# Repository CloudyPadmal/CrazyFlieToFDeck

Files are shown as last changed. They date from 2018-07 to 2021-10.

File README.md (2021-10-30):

# CrazyFlieToFDeck

This repository contains KiCAD source files and generated gerber files for **CrazyFlie Obstacle Avoidance Sensor Deck**.



<table>
<tr>
<th>Front View</td>
<th>Bottom View</td>
</tr>
<tr>
<td></td>
<td></td>
</tr>
</table>

## Time of Flight Sensor



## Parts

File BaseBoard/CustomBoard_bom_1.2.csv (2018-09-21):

Component | Description | Part | References | Value | Footprint | Quantity Per PCB | Datasheet
1 | Unpolarized capacitor | C_Small | C1 C2 | 100n | C_0603 | 2
2 | Unpolarized capacitor | C_Small | C3 | 4.7u | C_0603 | 1
3 | LED generic, alternativ symbol | LED_ALT | D1 | POWER_LED | LED_0603 | 1
4 | Generic connector, single row, 01x05 | Conn_01x05 | J15 | Camera | AMGCam | 1
5 | Generic connector, single row, 01x10 | Conn_01x10 | J2 | LEFT | BF090-10-X-B2 | 1
6 | Generic connector, single row, 01x10 | Conn_01x10 | J1 | RIGHT | BF090-10-X-B2 | 1
7 | Generic connector, single row, 01x05 | Conn_01x05 | J3 | Sensor01 | SensorPads | 1
8 | Generic connector, single row, 01x05 | Conn_01x05 | J4 | Sensor02 | SensorPads | 1
9 | Generic connector, single row, 01x05 | Conn_01x05 | J5 | Sensor03 | SensorPads | 1
10 | Generic connector, single row, 01x05 | Conn_01x05 | J6 | Sensor04 | SensorPads | 1
11 | Generic connector, single row, 01x05 | Conn_01x05 | J7 | Sensor05 | SensorPads | 1
12 | Generic connector, single row, 01x05 | Conn_01x05 | J8 | Sensor06 | SensorPads | 1
13 | Generic connector, single row, 01x05 | Conn_01x05 | J9 | Sensor07 | SensorPads | 1
14 | Generic connector, single row, 01x05 | Conn_01x05 | J10 | Sensor08 | SensorPads | 1
15 | Generic connector, single row, 01x05 | Conn_01x05 | J11 | Sensor09 | SensorPads | 1
16 | Generic connector, single row, 01x05 | Conn_01x05 | J12 | Sensor10 | SensorPads | 1
17 | Generic connector, single row, 01x05 | Conn_01x05 | J13 | Sensor11 | SensorPads | 1
18 | Generic connector, single row, 01x05 | Conn_01x05 | J14 | Sensor12 | SensorPads | 1
19 | Resistor | R | R2 R3 R4 R5 R6 R7 R8 R9 R10 R11 R12 R13 R14 | 10k | R_0603 | 13
20 | Resistor | R | R1 | 2k | R_0603 | 1
21 |  | DS28E05 | U1 | DS28E05 | SOT-23 | 1
22 |  | PCA9555X | U2 | PCA9555X | TSSOP-24_4.4x7.8mm_Pitch0.65mm | 1 | https://www.mouser.com/datasheet/2/302/PCA9555A-1127572.pdf
23 |  | VL53L1X | U3 | VL53L1X | VL53L1X | 1
Component Groups: | 23
Component Count: | 36
Fitted Components: | 36
Number of PCBs: | 1
Total components: | 36
Schematic Version: | 1.2
Schematic Date: | 2018-07-24
BoM Date: | Sat 11 Aug 2018 04:17:48 PM +0530
Schematic Source: | /home/knight/Documents/KiCAD/FinalBoards/CrazyFlieCustomBoardBase/CustomBoard.sch
KiCad Version: | Eeschema 4.0.7-e2-6376~58~ubuntu16.04.1

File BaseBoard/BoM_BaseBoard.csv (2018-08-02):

Component | Description | Part | References | Value | Footprint | Quantity Per PCB | Datasheet
1 | Unpolarized capacitor | C_Small | C1 C2 | 100n | C_0402 | 2
2 | Unpolarized capacitor | C_Small | C3 | 4.7u | C_0402 | 1
3 | LED generic, alternativ symbol | LED_ALT | D1 | POWER_LED | LED_0402 | 1
5 | Generic connector, single row, 01x10 | Conn_01x10 | J2 | LEFT | BF090-10-X-B2 | 1
6 | Generic connector, single row, 01x10 | Conn_01x10 | J1 | RIGHT | BF090-10-X-B2 | 1
19 | Resistor | R | R2 R3 R4 R5 R6 R7 R8 R9 R10 R11 R12 R13 R14 | 10k | R_0402 | 13
20 | Resistor | R | R1 | 2k | R_0402 | 1
21 |  | DS28E05 | U1 | DS28E05 | SOT-23 | 1
22 |  | PCA9555 | U2 | PCA9555 | QFN-24_4x4mm_Pitch0.5mm | 1
23 |  | VL53L1X | U3 | VL53L1X | VL53L1X | 1
Component Groups: | 23
Component Count: | 36
Fitted Components: | 36
Number of PCBs: | 1
Total components: | 36
Schematic Version: | 1.2

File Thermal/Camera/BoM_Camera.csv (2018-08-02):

Component | Description | Part | References | Value | Footprint | Quantity Per PCB | Datasheet
1 | Unpolarized capacitor | C_Small | C3 | 1.5u | C_0603 | 1
2 | Unpolarized capacitor | C_Small | C1 | 10u | C_0603 | 1
3 | Unpolarized capacitor | C_Small | C2 | 1u | C_0603 | 1
7 | Resistor | R | R1 R2 R3 | 10k | R_0402 | 3
8 | Resistor | R | R4 | 20R | R_0402 | 1
9 | Camera module | AMG8833 | U1 | AMG8833 | AMG8833 | 1
Component Groups: | 9
Component Count: | 11
Fitted Components: | 11
Number of PCBs: | 1
Total components: | 11

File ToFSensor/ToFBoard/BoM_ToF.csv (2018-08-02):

Component | Description | Part | References | Value | Footprint | Quantity Per PCB | Datasheet
1 | Unpolarized capacitor | C_Small | C1 | 100n | C_0402 | 1
2 | Unpolarized capacitor | C_Small | C2 | 4.7u | C_0402 | 1
5 | ToF sensor | VL53L1X | U1 | VL53L1X | VL53L1X | 1
Component Groups: | 5
Component Count: | 5
Fitted Components: | 5
Number of PCBs: | 1
Total components: | 5

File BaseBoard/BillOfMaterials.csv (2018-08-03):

Designator | MPN/Seed SKU | Qty | Price | Total
C6 | GRM033R60J155ME14EA01 | 1 | 0.33 | 0.33
C1 C2 C7 C9 C11 C13 C15 C17 C19 C21 C23 C25 C27 C29 C31 C33 C35 | CBR04C108B5GAC | 17 | 0.056 | 0.952
C4 | C1608X5R0J106K080AE | 1 | 0.32 | 0.32
C5 | 885012106003 | 1 | 0.1 | 0.1
C3 C8 C10 C12 C14 C16 C18 C20 C22 C24 C26 C28 C30 C32 C34 C36 | C1005X5R0J475K050BC | 16 | 0.35 | 5.6
D1 | SMLP13BC8TT86 | 1 | 0.4 | 0.4
J2 | BF090-10-X-B2 | 1 | 0.5 | 0.5
J1 | BF090-10-X-B2 | 1 | 0.5 | 0.5
R2 R3 R4 R5 R6 R7 R8 R9 R10 R11 R12 R13 R14 R15 R16 R17 | RT0402BRC0710KL | 16 | 0.349 | 5.584
R18 | RCS040220R0FKED | 1 | 0.11 | 0.11
R1 | CRCW04022K00JNEDC | 1 | 0.1 | 0.1
U4 | AMG8833 | 1 | 22.16 | 22.16
U1 | DS28E05R+T | 1 | 0.88 | 0.88
U2 | PCA9555BS,118 | 1 | 2.14 | 2.14
U3 U5 U6 U7 U8 U9 U10 U11 U12 U13 U14 U15 U16 U17 U18 U19 | VL53L1CXV0FY/1 | 16 | 5.81 | 92.96
 |  |  |  | 132.636

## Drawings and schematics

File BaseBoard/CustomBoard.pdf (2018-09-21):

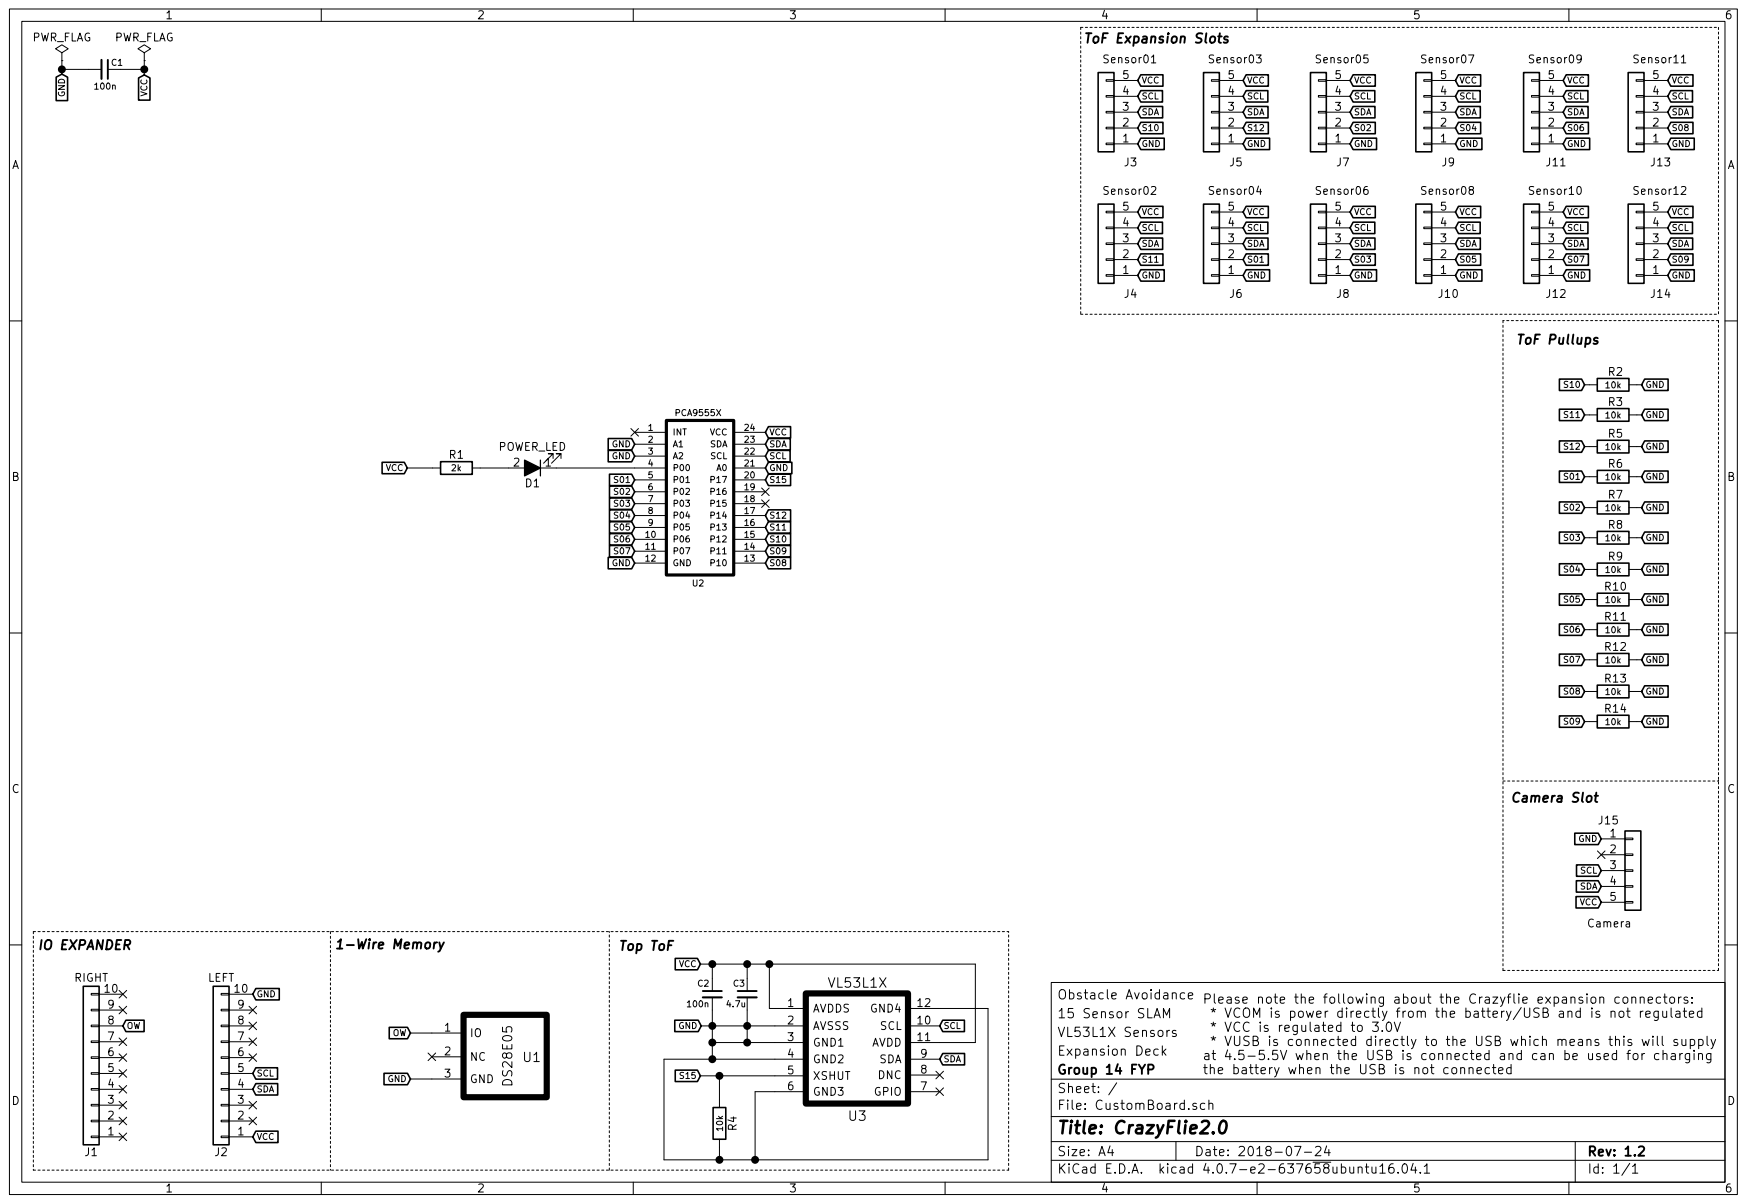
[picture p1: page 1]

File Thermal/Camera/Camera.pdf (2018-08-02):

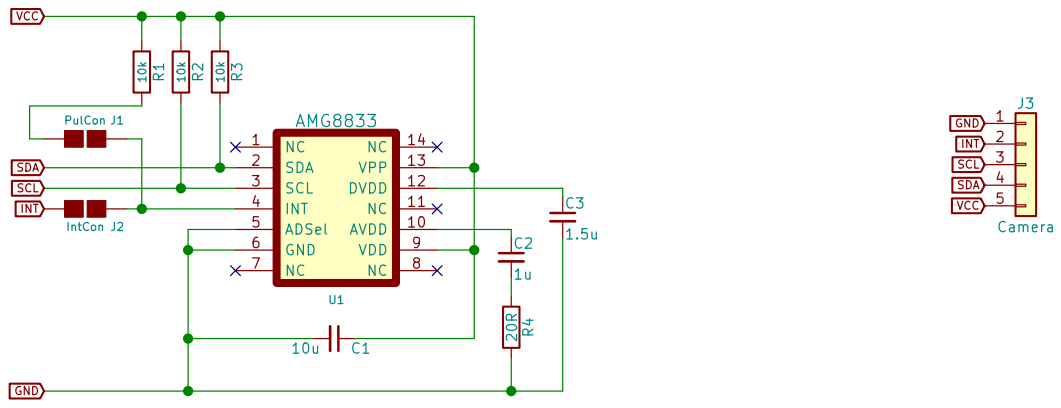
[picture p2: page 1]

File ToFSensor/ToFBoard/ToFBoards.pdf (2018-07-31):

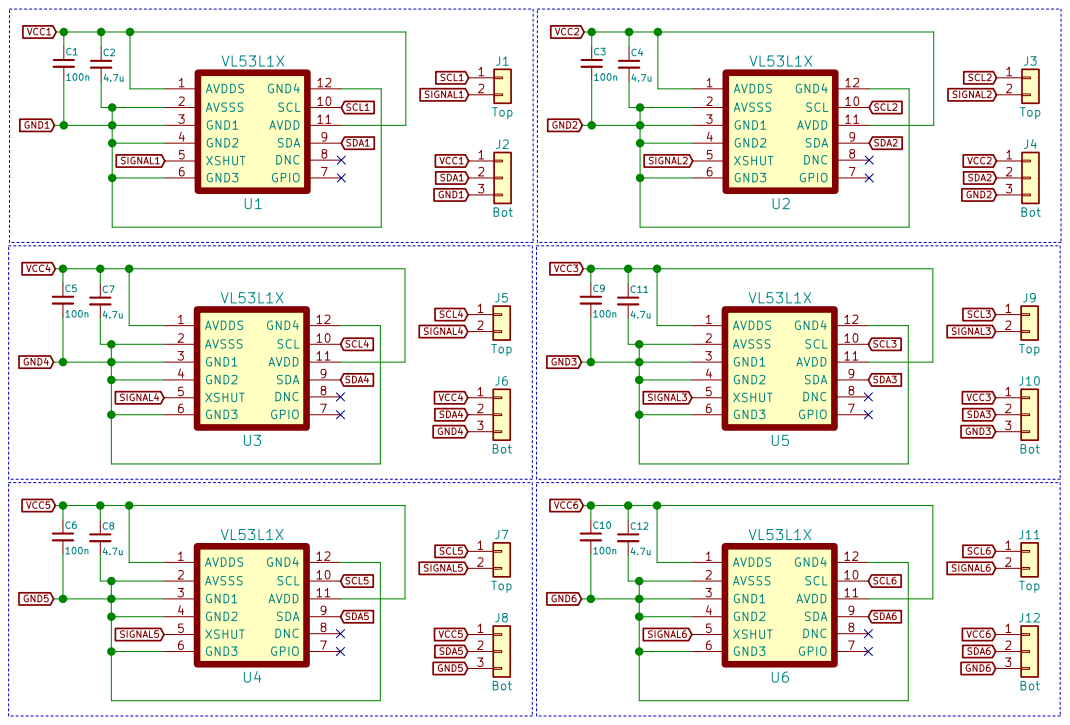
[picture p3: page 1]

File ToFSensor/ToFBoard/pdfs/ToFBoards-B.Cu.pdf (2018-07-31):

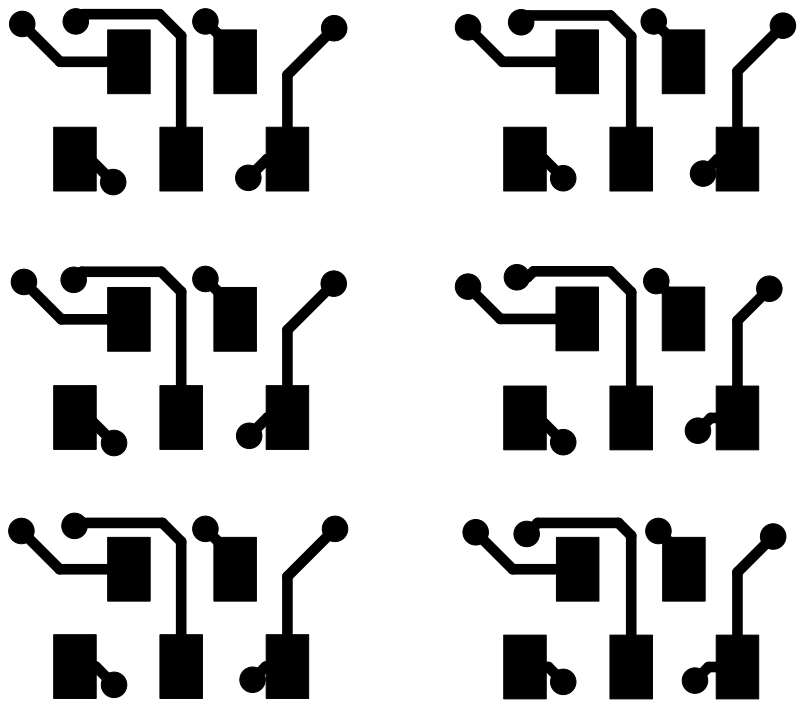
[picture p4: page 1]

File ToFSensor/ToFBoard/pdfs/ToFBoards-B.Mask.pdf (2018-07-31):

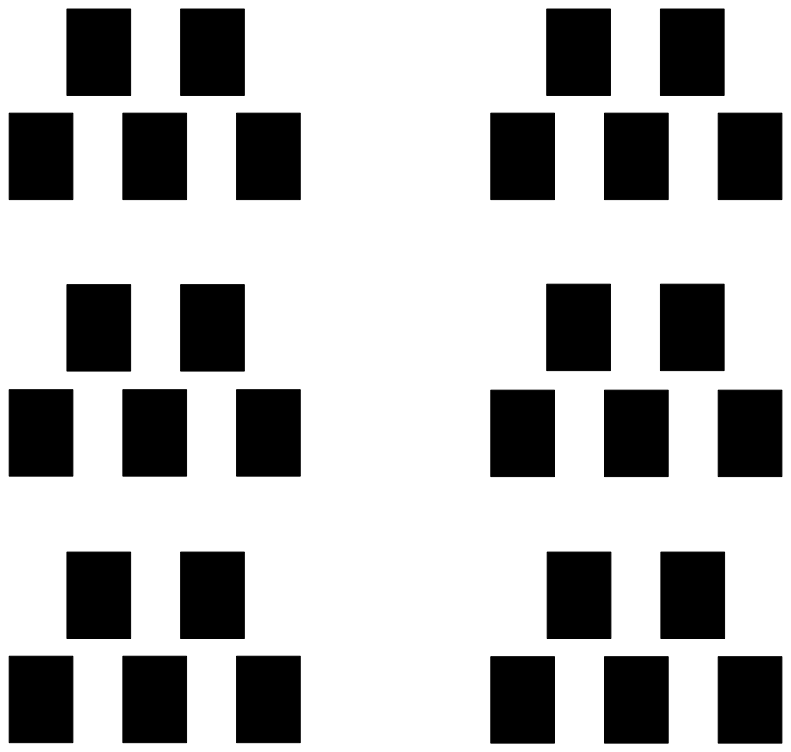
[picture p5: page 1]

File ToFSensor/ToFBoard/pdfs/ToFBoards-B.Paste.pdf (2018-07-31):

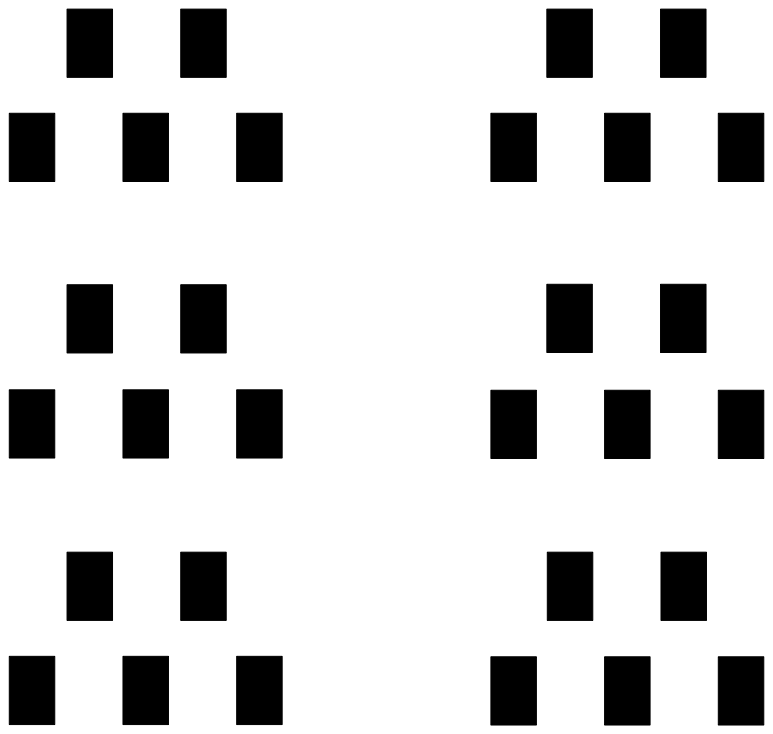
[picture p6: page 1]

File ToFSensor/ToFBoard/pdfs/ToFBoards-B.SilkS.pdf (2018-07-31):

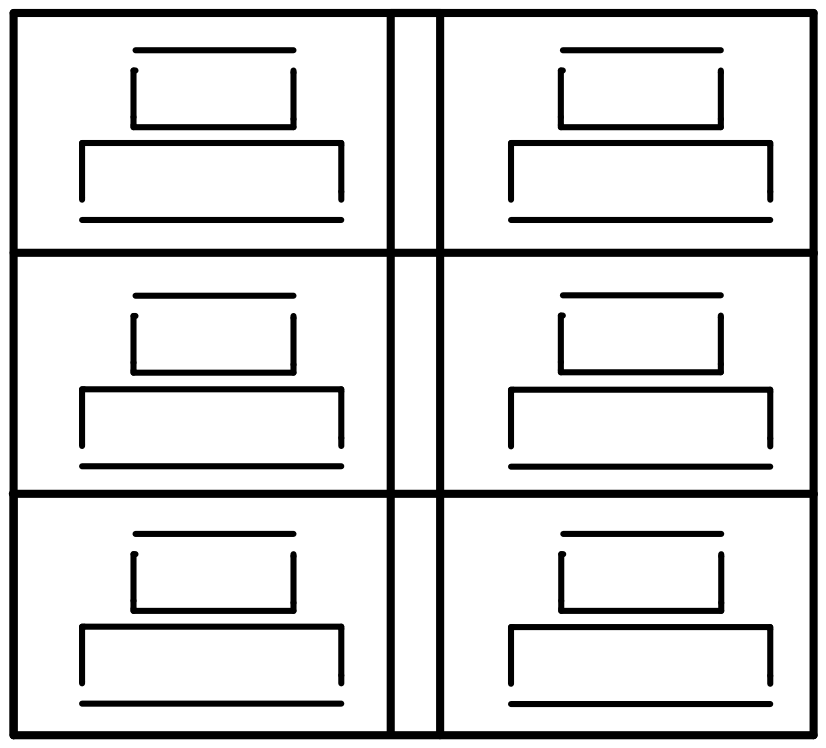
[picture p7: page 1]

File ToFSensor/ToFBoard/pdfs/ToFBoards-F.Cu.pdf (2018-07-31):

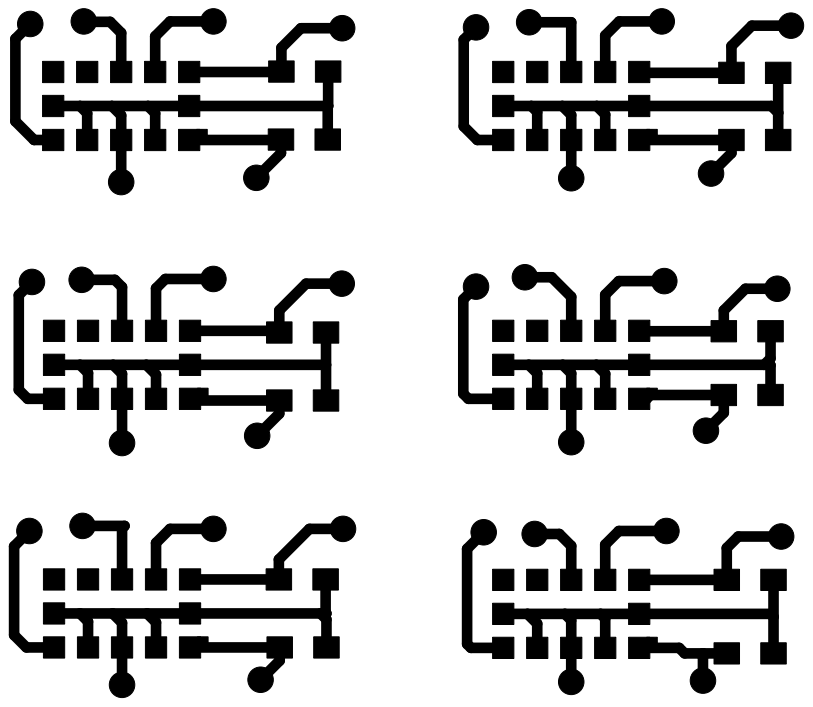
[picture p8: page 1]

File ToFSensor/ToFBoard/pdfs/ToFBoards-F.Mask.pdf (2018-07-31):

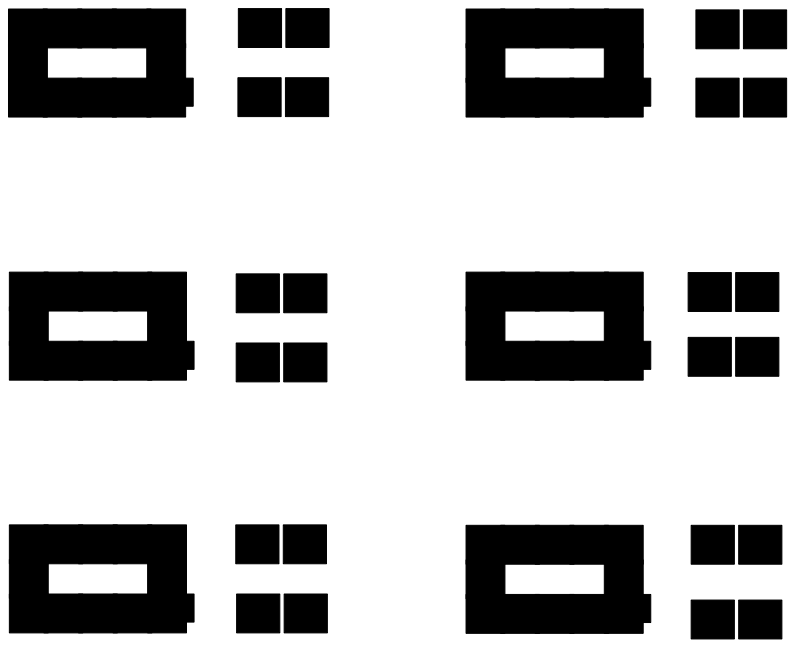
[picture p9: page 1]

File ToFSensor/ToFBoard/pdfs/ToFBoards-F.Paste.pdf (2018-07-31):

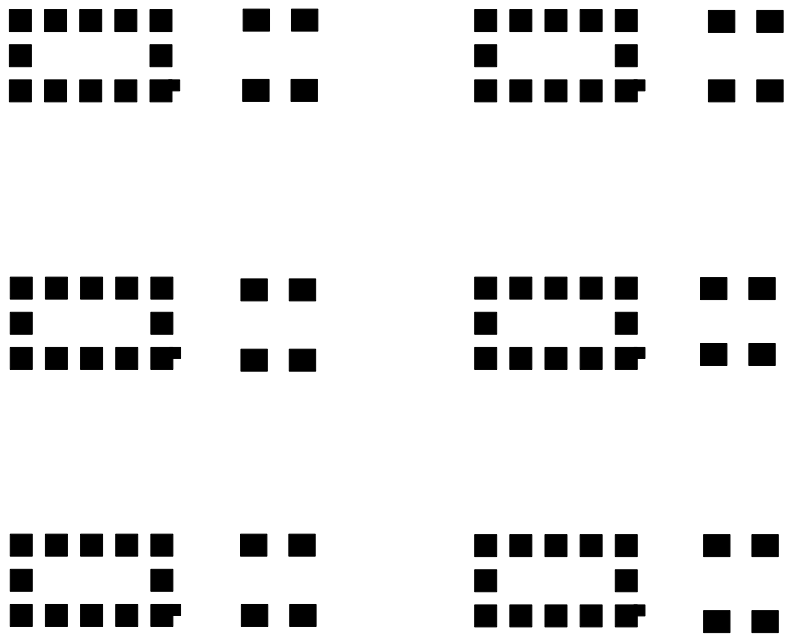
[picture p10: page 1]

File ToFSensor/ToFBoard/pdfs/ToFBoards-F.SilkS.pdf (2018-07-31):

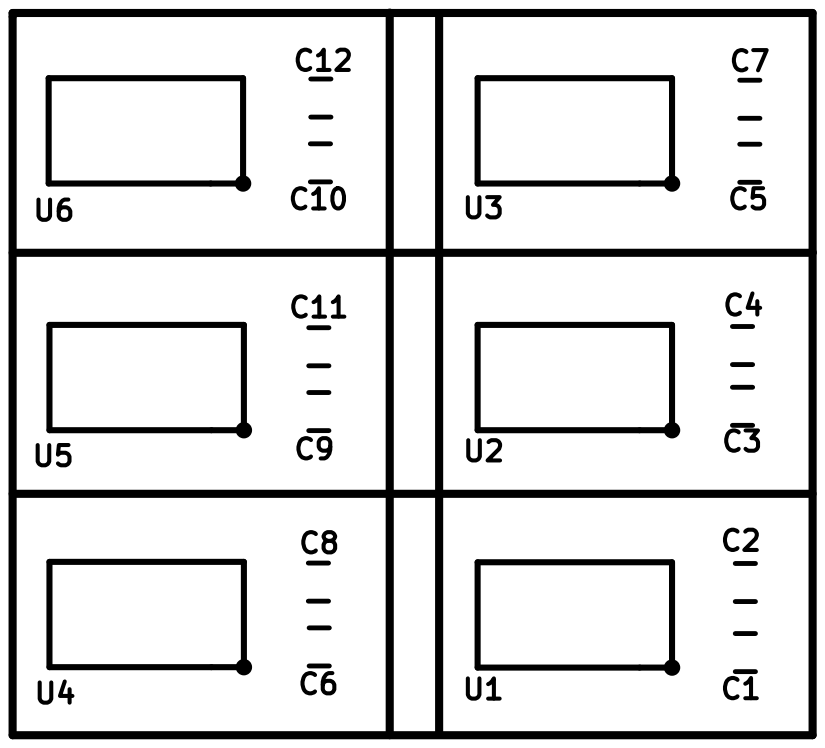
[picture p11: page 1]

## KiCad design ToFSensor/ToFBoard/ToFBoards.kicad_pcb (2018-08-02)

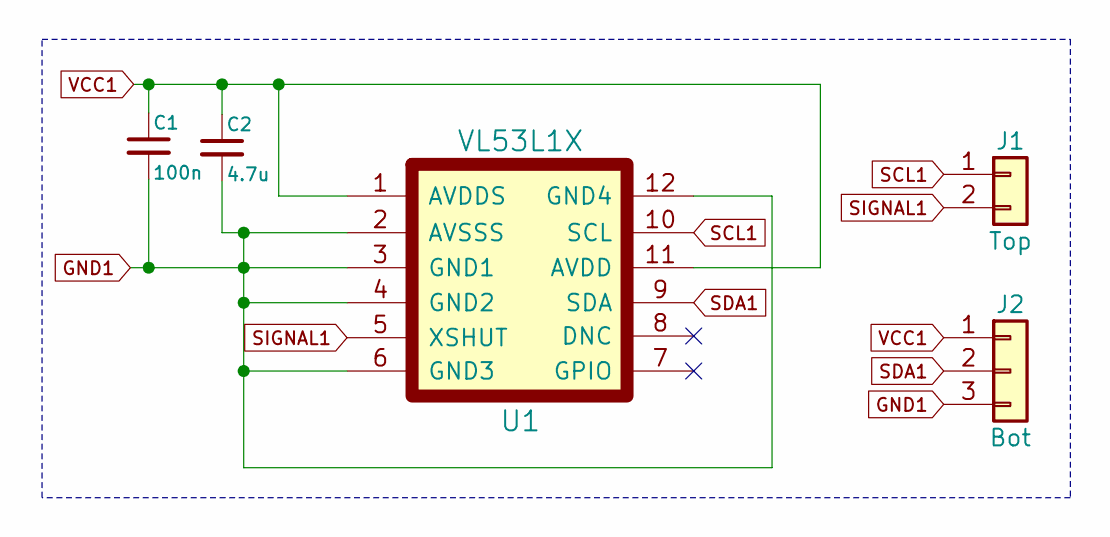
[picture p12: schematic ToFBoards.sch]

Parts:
C1: 100n; C_0402
C2: 4.7u; C_0402
J1: Top; ToFTop
J2: Bot; ToFBottom
U1: VL53L1X

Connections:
GND1: C1.2, C2.2, J2.3, U1.2 (AVSSS), U1.3 (GND1), U1.4 (GND2), U1.6 (GND3), U1.12 (GND4)
SCL1: J1.1, U1.10 (SCL)
SDA1: J2.2, U1.9 (SDA)
SIGNAL1: J1.2, U1.5 (XSHUT)
VCC1: C1.1, C2.1, J2.1, U1.1 (AVDDS), U1.11 (AVDD)

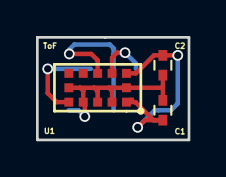
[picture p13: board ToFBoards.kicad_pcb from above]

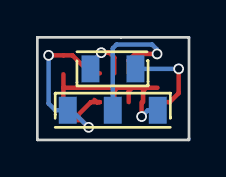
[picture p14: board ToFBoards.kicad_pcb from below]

Board: 2 copper layers, 8.4 x 5.7 mm, 5 parts (2 on the bottom side), 5 nets.

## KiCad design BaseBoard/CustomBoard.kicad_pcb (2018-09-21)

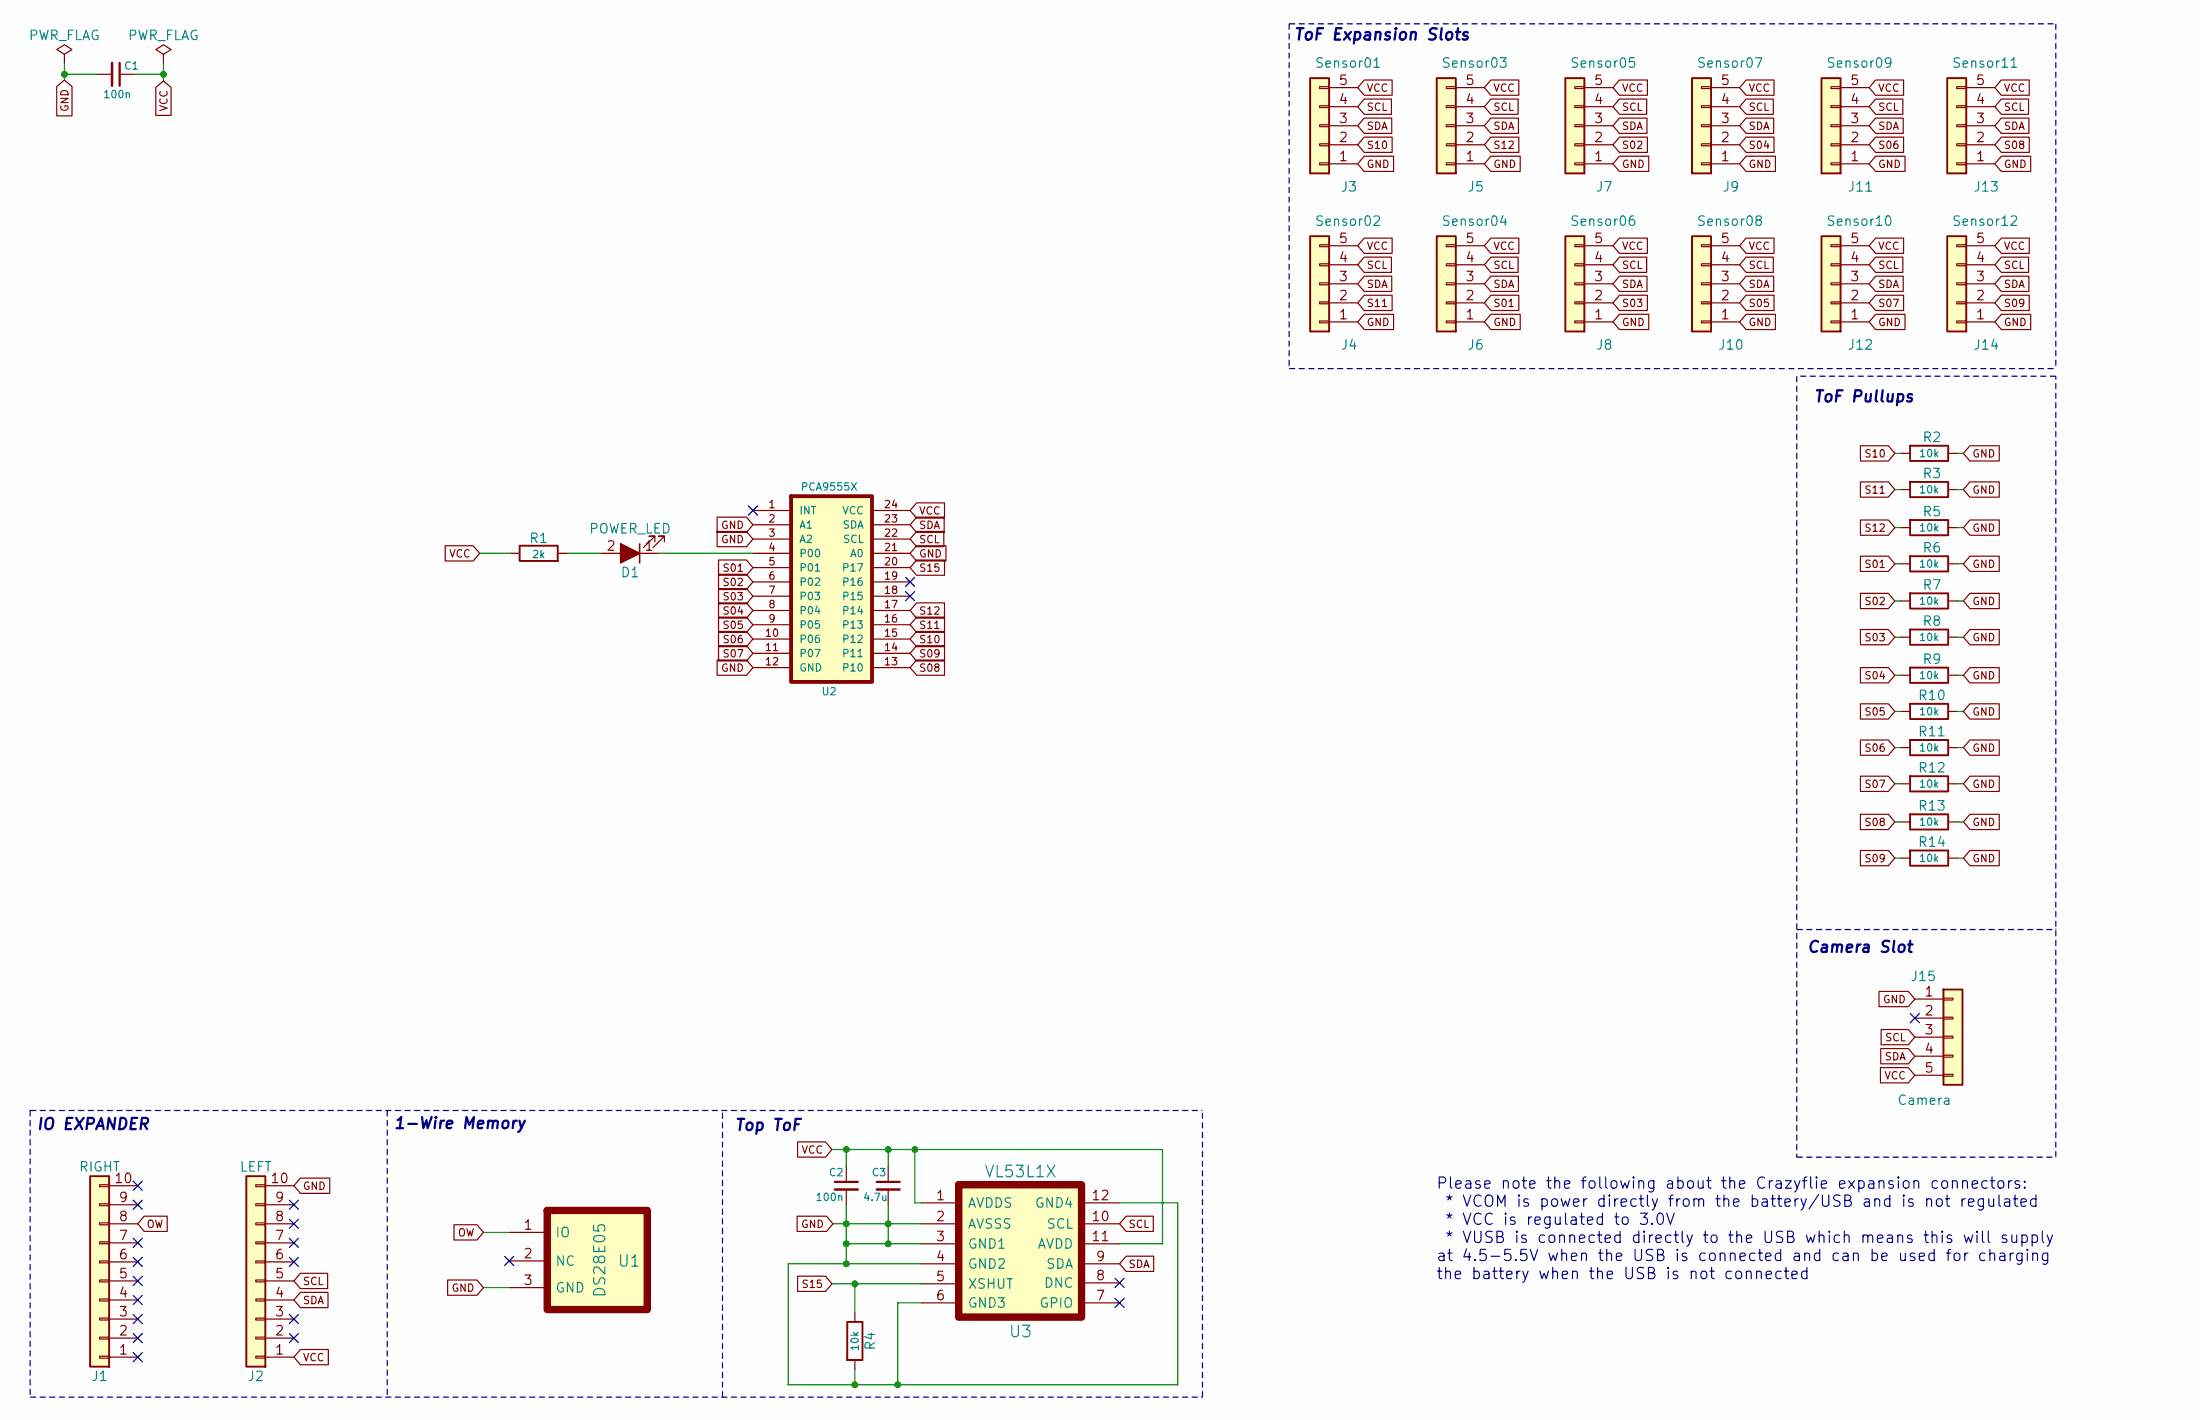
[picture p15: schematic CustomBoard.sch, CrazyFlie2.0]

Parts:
C1, C2: 100n; C_0603
C3: 4.7u; C_0603
D1: POWER_LED; LED_0603
J1: RIGHT; BF090-10-X-B2
J2: LEFT; BF090-10-X-B2
J3: Sensor01; SensorPads
J4: Sensor02; SensorPads
J5: Sensor03; SensorPads
J6: Sensor04; SensorPads
J7: Sensor05; SensorPads
J8: Sensor06; SensorPads
J9: Sensor07; SensorPads
J10: Sensor08; SensorPads
J11: Sensor09; SensorPads
J12: Sensor10; SensorPads
J13: Sensor11; SensorPads
J14: Sensor12; SensorPads
J15: Camera; AMGCam
R1: 2k; R_0603
R2, R3, R4, R5, R6, R7, R8, R9, R10, R11, R12, R13, R14: 10k; R_0603
U1: DS28E05; SOT-23
U2: PCA9555X; TSSOP-24_4.4x7.8mm_Pitch0.65mm
U3: VL53L1X

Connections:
GND: C1.2, C2.2, C3.2, J2.10, J3.1, J4.1, J5.1, J6.1, J7.1, J8.1, J9.1, J10.1, J11.1, J12.1, J13.1, J14.1, J15.1, R2.1, R3.1, R4.2, R5.1, R6.1, R7.1, R8.1, R9.1, R10.1, R11.1, R12.1, R13.1, R14.1, U1.3 (GND), U2.2 (A1), U2.3 (A2), U2.12 (GND), U2.21 (A0), U3.2 (AVSSS), U3.3 (GND1), U3.4 (GND2), U3.6 (GND3), U3.12 (GND4)
unnamed: D1.1 (K), U2.4 (P00)
unnamed: D1.2 (A), R1.2
OW: J1.8, U1.1 (IO)
S01: J6.2, R6.2, U2.5 (P01)
S02: J7.2, R7.2, U2.6 (P02)
S03: J8.2, R8.2, U2.7 (P03)
S04: J9.2, R9.2, U2.8 (P04)
S05: J10.2, R10.2, U2.9 (P05)
S06: J11.2, R11.2, U2.10 (P06)
S07: J12.2, R12.2, U2.11 (P07)
S08: J13.2, R13.2, U2.13 (P10)
S09: J14.2, R14.2, U2.14 (P11)
S10: J3.2, R2.2, U2.15 (P12)
S11: J4.2, R3.2, U2.16 (P13)
S12: J5.2, R5.2, U2.17 (P14)
S15: R4.1, U2.20 (P17), U3.5 (XSHUT)
SCL: J2.5, J3.4, J4.4, J5.4, J6.4, J7.4, J8.4, J9.4, J10.4, J11.4, J12.4, J13.4, J14.4, J15.3, U2.22 (SCL), U3.10 (SCL)
SDA: J2.4, J3.3, J4.3, J5.3, J6.3, J7.3, J8.3, J9.3, J10.3, J11.3, J12.3, J13.3, J14.3, J15.4, U2.23 (SDA), U3.9 (SDA)
VCC: C1.1, C2.1, C3.1, J2.1, J3.5, J4.5, J5.5, J6.5, J7.5, J8.5, J9.5, J10.5, J11.5, J12.5, J13.5, J14.5, J15.5, R1.1, U2.24 (VCC), U3.1 (AVDDS), U3.11 (AVDD)

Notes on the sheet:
IO EXPANDER
Please note the following about the Crazyflie expansion connectors: * VCOM is power directly from the battery/USB and is not regulated * VCC is regulated to 3.0V * VUSB is connected directly to the USB which means this will supply at 4.5-5.5V when the USB is connected and can be used for charging t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
1-Wire Memory
ToF Expansion Slots
Top ToF
Camera Slot
ToF Pullups

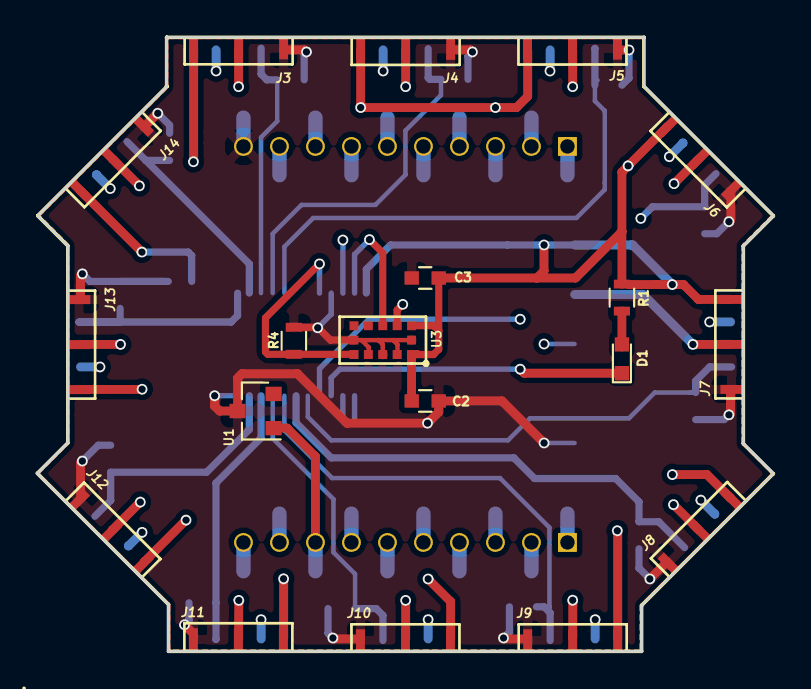
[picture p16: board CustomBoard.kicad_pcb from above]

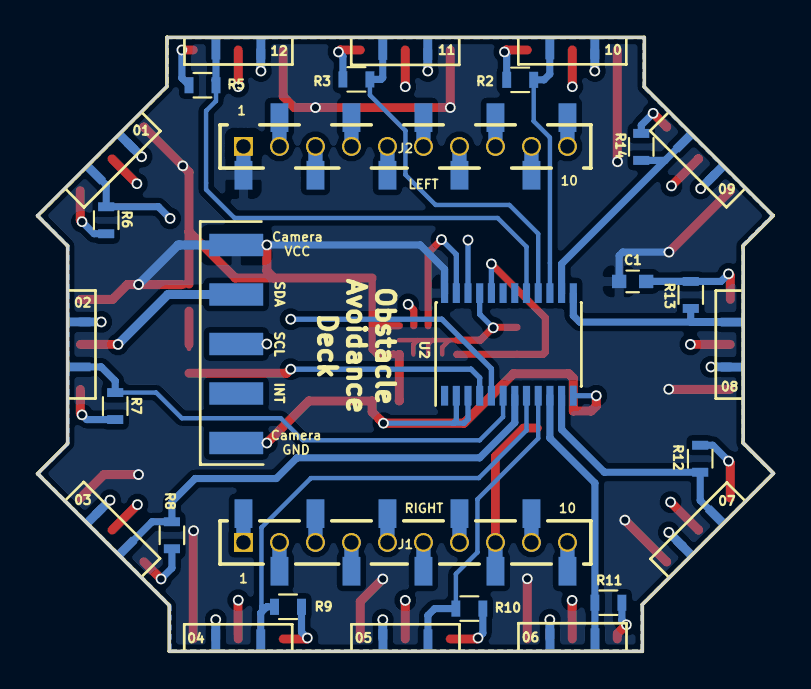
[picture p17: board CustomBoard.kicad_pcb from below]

Board: 4 copper layers, 40.9 x 34.1 mm, 36 parts (17 on the bottom side), 20 nets.

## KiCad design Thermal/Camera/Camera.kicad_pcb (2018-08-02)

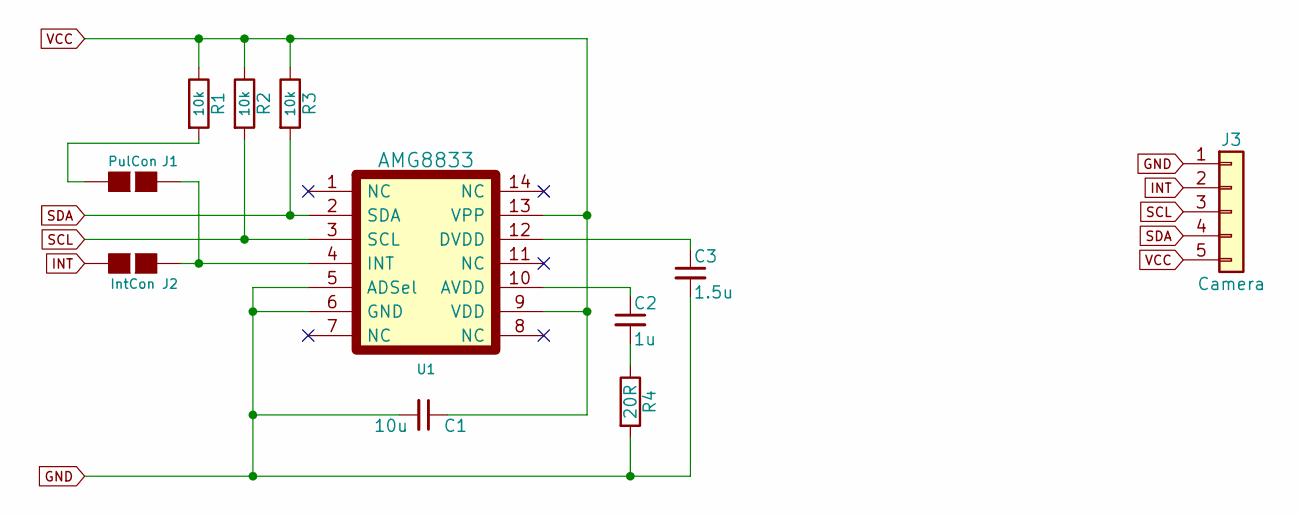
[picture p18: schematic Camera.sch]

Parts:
C1: 10u; C_0603
C2: 1u; C_0603
C3: 1.5u; C_0603
J1: PulCon; GS2
J2: IntCon; GS2
J3: Camera; AMGCam
R1, R2, R3: 10k; R_0402
R4: 20R; R_0402
U1: AMG8833

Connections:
GND: C1.2, C3.2, J3.1, R4.2, U1.5 (ADSel), U1.6 (GND)
INT: J2.2 (G2), J3.2
unnamed: C2.1, U1.10 (AVDD)
unnamed: C2.2, R4.1
unnamed: C3.1, U1.12 (DVDD)
unnamed: J1.1 (G1), R1.2
unnamed: J1.2 (G2), J2.1 (G1), U1.4 (INT)
SCL: J3.3, R2.2, U1.3 (SCL)
SDA: J3.4, R3.2, U1.2 (SDA)
VCC: C1.1, J3.5, R1.1, R2.1, R3.1, U1.9 (VDD), U1.13 (VPP)

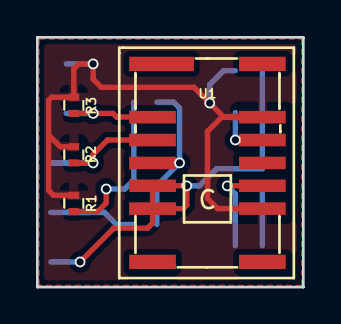
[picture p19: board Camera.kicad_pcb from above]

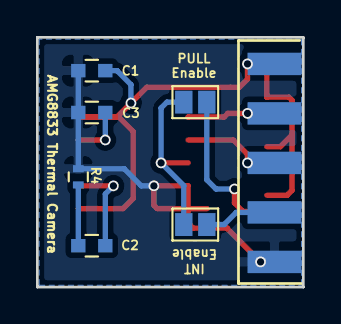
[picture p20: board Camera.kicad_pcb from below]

Board: 2 copper layers, 14.8 x 13.9 mm, 11 parts (7 on the bottom side), 10 nets.

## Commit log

2018-07-24 added deck expanders
    [CustomBoard.sch]
2018-07-25 pcb layout
    [CustomBoard.sch]
2018-07-25 pcb layout update
    [CustomBoard.kicad_pcb, CustomBoard.sch]
2018-07-25 datasheet for slam deck
    [CustomBoard.kicad_pcb]
2018-07-25 4m range ToF sensor parts
    [CustomBoard.kicad_pcb, CustomBoard.sch]
2018-07-26 new footprints
    [CustomBoard.kicad_pcb, CustomBoard.sch]
2018-07-27 dimensions fixed
    [CustomBoard.kicad_pcb, template-Eco1.User.dxf, template-Edge.Cuts.dxf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]
2018-07-27 routing started
    [CustomBoard.kicad_pcb]
2018-07-27 routing continues
    [CustomBoard.kicad_pcb]
2018-07-27 routing optimization
    [CustomBoard.kicad_pcb]
2018-07-30 adding 4 layers
    [CustomBoard.kicad_pcb]
2018-07-30 routing power lines
    [CustomBoard.kicad_pcb]
2018-07-30 pull ups
    [CustomBoard.sch]
2018-07-30 continue routing
    [CustomBoard.kicad_pcb, _saved_CustomBoard.sch]
2018-07-30 continue routing ..
    [CustomBoard.kicad_pcb]
2018-07-30 pads missing
    [CustomBoard-B.Cu.gbr, CustomBoard-B.Mask.gbr, CustomBoard-B.Paste.gbr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]
2018-07-30 saved state
    [_saved_CustomBoard.sch]
2018-07-31 footprints back
    [CustomBoard.kicad_pcb, _saved_CustomBoard.sch]
2018-07-31 footprints back all
    [CustomBoard.kicad_pcb]
2018-07-31 complete board
    [CustomBoard-A.SCL.gbr, CustomBoard-B.Cu.gbr, CustomBoard-B.Mask.gbr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]
2018-07-31 ToF boards
    [ToFBoards.kicad_pcb, ToFBoards.sch]
2018-07-31 complete ToF boards
    [ToFBoards.kicad_pcb, ToFBoards.sch]
2018-07-31 fix commit issues
    [ToFBoards-B.Cu.gbr, ToFBoards-B.Mask.gbr, ToFBoards-B.Paste.gbr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]
2018-07-31 camera module
    [CustomBoard.kicad_pcb]
2018-08-01 camera module pcb
    [Camera-B.Cu.gbr, Camera-B.Mask.gbr, Camera-B.Paste.gbr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]
2018-08-02 integrate cam module in main board
    [CustomBoard.kicad_pcb, CustomBoard.sch]
2018-08-02 gerber files
    [BoM_BaseBoard.csv, BoM_Camera.csv, BoM_ToF.csv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]
2018-08-03 update bom
    [BillOfMaterials.csv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]
2021-10-30 refactor: rearranged files into three folders
    [BillOfMaterials.csv, BoM_BaseBoard.csv, BoM_Camera.csv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]
